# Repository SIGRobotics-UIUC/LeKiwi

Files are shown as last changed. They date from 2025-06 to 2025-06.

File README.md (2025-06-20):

# LeKiwi
<div style="display: flex; justify-content: center; align-items: center; padding: 25px;">
    
    
    
    
</div>

> LeKiwi - Low-Cost Mobile Manipulator | Version 1

  

## Step by step tutorial
1. [Bill of Materials](BOM.md)
2. [3D Printing](3DPrinting.md)
3. [Assembly](Assembly.md)
4. [Get started with LeRobot](https://huggingface.co/docs/lerobot/lekiwi)

## Hardware Design
#### Standardized Stacked Base Plates
- Inspired by the [open robotic platform](https://openroboticplatform.com/designrules), our base plates have 3.5mm diameter holes spaced 20mm apart for standardized mounting

#### Power
- (12V version) 12v 5A Li-ion battery
- (5V version) 65W Laptop power bank

> [!TIP]  
> If this is the first time you build robots please choose the 5V version as it’s a little bit easier to assemble. If you are more experienced and want to lift heavier objects choose the 12V version. If you want to cheapest option possible go for the wired LeKiwi version.

#### Compute
- Raspberry Pi 5
- Streaming to a Laptop

#### Drive
- 3-wheel Kiwi (holonomic) drive with omni wheels

#### Robot Arm
- [SO-ARM101](https://github.com/TheRobotStudio/SO-ARM100)

#### Sensors
- Workspace rgb camera
- Wrist rgb camera

## Software Capabilities
Goals:
- Teleoperation with controller or laptop WASD + leader arm
- Data collection pipeline
- Streaming joint angles and camera feed

## CAD Design
[Fusion 360 CAD](https://a360.co/4k1P8yO)

We also provide the [URDF](./URDF/) exported from CAD for simulation.
## Get In Touch!

Join the project on LeRobot's [Discord server](https://discord.gg/Jtz5TJtb2u) (channel `mobile-so100-arm`)! Let us know if you have any questions, suggestions, or other feedback.

## Check out our Dynamixel Version!
We converted LeKiwi to use ROBOTIS components by using the Koch v1.1 arm, U2D2 motor controller, and Dynamixel XL430 motors for the mobile base.  [Dynamixel LeKiwi](DynamixelLeKiwi)

## Main Contributors
Thank you to everyone who helped on the project!

**CAD Design**: Manav Chandaka, Bhargav Chandaka, Pepijn Kooijmans

**Software**: Pepijn Kooijmans, Gloria Wang, Bhargav Chandaka, Advait Patel

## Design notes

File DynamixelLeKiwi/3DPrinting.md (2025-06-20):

# 3D Printing
> **Estimated time:** ~34 hours

We provide ready-to-print STL files for the 3D-printed parts below. These can be printed with generic PLA filament on consumer-grade FDM printers. We tested on a [Bambu Lab P1S](https://us.store.bambulab.com/products/p1s) printer. For all components, we just load into bambuslicer, auto-rotate and auto-arrange, enable any recommended supports, and print.

## Parts

| Item | Quantity | Notes | 
|:---|:---:|:---:|
| [Base plate Top](/3DPrintMeshes/base_plate_layer2.stl) | 1 | |
| [Base plate Bottom](/3DPrintMeshes/base_plate_layer1.stl) | 1 | |
| [Dynamixel Drive motor mount](3DPrintMeshes/dynamixel_drive_motor_mount.stl) | 3 | |
| [Dynamixel Servo wheel hub](/3DPrintMeshes/dynamixel_wheel_hub.stl) | 3 | Use Supports<sup>[1](#footnote1)</sup> |
| [Servo controller mount](/3DPrintMeshes/servo_controller_mount.stl) | 1 | |
| [12v Battery mount](/3DPrintMeshes/battery_mount.stl) **or** [12v EU Battery mount](/3DPrintMeshes/battery_mount_eu.stl) **or** [5v Battery mount](/3DPrintMeshes/5v_specific/5v_power_bank_holder.stl)| 1 | |
| [RasPi case Top](/3DPrintMeshes/pi_case_top.stl) | 1 | <sup>[2](#footnote2)</sup> |
| [RasPi case Bottom](/3DPrintMeshes/pi_case_bottom.stl) | 1 | <sup>[2](#footnote2)</sup> |
| Arducam [base mount](/3DPrintMeshes/base_camera_mount.stl) | 1 | **Compatible with [this camera](https://www.amazon.com/Arducam-Camera-Computer-Without-Microphone/dp/B0972KK7BC)** |
| Webcam [base mount](3DPrintMeshes/webcam_mount/webcam_mount.stl), [gripper insert](3DPrintMeshes/webcam_mount/so100_gripper_cam_mount_insert.stl) | 1 | **Compatible with [this camera](https://www.amazon.fr/Vinmooog-equipement-Microphone-Enregistrement-conférences/dp/B0BG1YJWFN/)** |
| [Modified Follower Arm Base](/3DPrintMeshes/dynamixel_modified_base_arm.stl) | 1 | Use Tree Supports, **Optional, but recommended if you have not built Koch already** |
| [Follower arm](https://github.com/jess-moss/koch-v1-1) | 1 | |
| [Leader arm](https://github.com/jess-moss/koch-v1-1) | 1 | |

> **Note**: Make sure to enable supports where specified!
<!-- > STL files are already oriented and ready-to-print.  -->

## Printing Instructions
Assuming you already have access to a 3D printer<sup>[3](#footnote3)</sup>, follow these steps to print all the parts above.

### 1. Setup Printer
1. Calibrate the printer and level beds according to printer-specific instructions
2. Clean the print bed
3. Load-in filament

### 2. Print the Parts
1. Upload STL file to printing/slicing software. Auto-rotate and auto-arrange. 
2. Enable supports if specified and slice. We tested with the following settings:
    - Infill Density: 15%
    - Layer Height: 0.2 mm
    - Printing Speed: 150 mm/s
3. If needed, upload G-code (slice file) to printer and print

### 3. Take Down
1. Remove printed part(s) from printer
2. Clean print bed if needed
3. Remove any supports from printed parts

> For tutorials on how to assemble the robot, checkout the [Assembly](Assembly.md) page!

## Footnotes
<a name="footnote1">1</a>: Modified from [VEX VersaHub model](https://www.vexrobotics.com/versahubs.html?srsltid=AfmBOooDKLcAfkuEgHyrjk24WFDrLTP4TQWkGjEpC-9HcyaMMCUMDSzs)

<a name="footnote2">2</a>: Modified from [Micro Center model](https://www.printables.com/model/605060-raspberry-pi-5-case-wpower-button-v2)

<a name="footnote3">3</a>: If not, we recommend [Bambu Lab](https://bambulab.com/en-us) or [Prusa](https://www.prusa3d.com/), or checkout this [list of brands](https://github.com/ad-si/awesome-3d-printing?tab=readme-ov-file#3d-printer-brands).

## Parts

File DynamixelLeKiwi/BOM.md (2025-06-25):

# Bill of Materials

This page provides a complete list of parts needed to build the Dynamixel LeKiwi mobile manipulator. Our total cost is displayed in the table <sup>[1](#footnote1)</sup>.

| Price| US  | EU  | CN |
|---|----:|----:|----:|
| **Dynamixel LeKiwi** |  **$797.47**  |  **€1035.3**  |  **¥5938**  ||
| **Base only** |  **$320.47**  |  **€362.3**  |  **¥1991.28**  |

> [!NOTE] 
> Prices and items may vary depending on geographic location and time of purchase. If you find links for other countries or cheaper suppliers, please create an issue or PR so that we add them to the list!

### Mobile Base Structure:
| Part | Amount | Unit Cost (US) | Buy (US) | Unit Cost (EU) | Buy (EU) | Unit Cost (CN) | Buy (CN) |
| - | - | - | - | - | - | - | - |
| 4" Omni wheels | 3 | $9.99 | [VEX Robotics](https://www.vexrobotics.com/omni-wheels.html?srsltid=AfmBOorWdWT-FIiWSAbicYWSxqYr-d5X3CJSGxMkO33WO0thwlTn4DQu) | €24.5 | [RobotShop](https://eu.robotshop.com/products/100mm-omnidirectional-wheel-brass-bearing-rollers) |￥135 |[PDD](https://mobile.yangkeduo.com/goods.html?ps=kKWPC7xuzw "https://mobile.yangkeduo.com/goods.html?ps=kKWPC7xuzw")|
| M2 M3 M4 Assorted Screw Set | 1 | $14.99 | [Amazon](https://www.amazon.com/Button-Socket-Washers-Assortment-Machine/dp/B0BMQGJP3F) | €23.5 | [Amazon](https://www.amazon.fr/Cylindrique-Inoxydable-M2-Socket-Assortiment/dp/B09Y8WYFWD/) |￥25 |[Taobao（M2x5+M3套装+M3x10+M4x12）](https://e.tb.cn/h.64O1J2A9Is4pIJd "https://e.tb.cn/h.64O1J2A9Is4pIJd") |
| **Total** || **$44.96** || **€97** || **¥430** ||

### Sensors and Compute:

| Part| Amount | Unit Cost (US) | Buy (US) | Unit Cost (EU) | Buy (EU) |  Unit Cost (CN) | Buy (CN) |
|--|:-:|:-:|-|:-:|-|:-:|-|
| Raspberry Pi 5 (4GB)| 1 |$60.00| [Adafruit](https://www.adafruit.com/product/5812)| €57.00| [Mouser](https://eu.mouser.com/ProductDetail/Raspberry-Pi/SC1111?qs=HoCaDK9Nz5fnLhlMNnKTiQ%3D%3D)|￥410|[Taobao](https://e.tb.cn/h.64IIvlisvAL15g8?tk=fdOVexkHECW "https://e.tb.cn/h.64IIvlisvAL15g8?tk=fdOVexkHECW")|
| USB camera<sup>[2](#footnote2)</sup> | 2 | $12.98 | [Amazon](https://a.co/d/236G8Wn) | €12.00 | [Amazon](https://www.amazon.fr/Vinmooog-equipement-Microphone-Enregistrement-conf%C3%A9rences/dp/B0BG1YJWFN/) |￥48|[Taobao](https://e.tb.cn/h.64ILq3suMKATfUx?tk=IPSEexQAvxu "https://e.tb.cn/h.64ILq3suMKATfUx?tk=IPSEexQAvxu")|
| microSD card | 1 | $11.23 | [Amazon](https://www.amazon.com/SanDisk-Extreme-microSDXC-Memory-Adapter/dp/B09X7C7LL1/) | €10.00 | [Amazon](https://www.amazon.fr/Lexar-Carte-Micro-adaptateur-Smartphone/dp/B08XZ2KS1F)|￥58|[Taobao](https://e.tb.cn/h.64DMZzLz5h26s12?tk=eImPex96lCQ "https://e.tb.cn/h.64DMZzLz5h26s12?tk=eImPex96lCQ")|
| U2D2_INT | 1 | $32.10 | [ROBOTIS](https://en.robotis.com/shop_en/item.php?it_id=902-0132-000) | €27.93 | [ROBOTIS](https://en.robotis.com/shop_en/item.php?it_id=902-0132-000)|￥230.73|[ROBOTIS](https://en.robotis.com/shop_en/item.php?it_id=902-0132-000)|
| U2D2 PHB | 1 | $19.00 | [ROBOTIS](https://en.robotis.com/shop_en/item.php?it_id=902-0145-001) | €16.53 | [ROBOTIS](https://en.robotis.com/shop_en/item.php?it_id=902-0145-001)|￥136.57|[ROBOTIS](https://en.robotis.com/shop_en/item.php?it_id=902-0145-001)|
| **Total** ||  **$135.31**  ||  **€123.46** ||  **¥883.3** ||

### Other
| Part| Amount | Unit Cost (US) | Buy (US) | Unit Cost (EU) | Buy (EU) | Unit Cost (CN) | Buy (CN) |
|--|:-:|:-:|-|:-:|-|:-:|-|
| Table Clamp 4pcs | 1 | $18 | [Amazon](https://www.amazon.com/WORKPRO-Clamps-Woodworking-One-Handed-Spreader/dp/B0CQYDJWS8/) | € 21 | [Amazon](https://www.amazon.fr/dp/B08HW9VFM8/)| ¥10.8\*4  |[Taobao](https://e.tb.cn/h.64r5eomI6L59tBE?tk=gZWeex9fnlB "https://e.tb.cn/h.64r5eomI6L59tBE?tk=gZWeex9fnlB")|
| Screwdriver Set | 1 | $6 | [Amazon](https://www.amazon.com/Precision-Phillips-Screwdriver-Electronics-Computer/dp/B0DB227RTH) | €10 | [Amazon](https://www.amazon.fr/dp/B08ZXVMVYD/) | ￥20 |[Taobao](https://e.tb.cn/h.6ReL0wwgtPuSmNV?tk=3rLDV10AVtr)  |
| USB-C to USB-A Cable 2 pcs | 1 | $7 | [Amazon](https://www.amazon.com/Charging-etguuds-Charger-Braided-Compatible/dp/B0B8NWLLW2/?th=1) | €7 | [Amazon](https://www.amazon.fr/dp/B07BNF842T/) |￥17  |[Taobao](https://e.tb.cn/h.64HOv24RLmYC4Yh?tk=AXpgexkDFd4 "https://e.tb.cn/h.64HOv24RLmYC4Yh?tk=AXpgexkDFd4")|
| **Total** ||  **$31**  ||  **€38** || **¥80.20** ||

### Mobile Base Electronics
| Part | Amount | Unit Cost (US) | Buy (US) | Unit Cost (EU) | Buy (EU) | Unit Cost (CN) | Buy (CN) |
|:---|:---:|:---:|:---|:---:|---:|:-:|-|
| 12v 5a Battery | 1 | $32.99 | [Amazon](https://www.amazon.com/KBT-Rechargeable-Connector-Replacement-Security/dp/B0C242DYT1/ref=sr_1_2_sspa?) | €45.79 | [Amazon](https://www.amazon.fr/dp/B0D5QSMW21) | ￥70 |[Taobao](https://e.tb.cn/h.64IJNTnXwhn44BS?tk=PQQ8exkJEtR "https://e.tb.cn/h.64IJNTnXwhn44BS?tk=PQQ8exkJEtR")|
| Lever Wire Connector | 1 | $6.70 | [Amazon](https://www.amazon.com/Wago-221-413-LEVER-NUTS-Conductor-Connectors/dp/B06XGYXVXR/ref=sr_1_4) | €7.18 | [Amazon](https://www.amazon.fr/221-413-fil-électrique-connecteur-220-240-Terminal/dp/B01AKF3I58) | ￥3.50 |[Taobao](https://e.tb.cn/h.64r0Z6Y5jZczq5q?tk=XEaSex908q0 "https://e.tb.cn/h.64r0Z6Y5jZczq5q?tk=XEaSex908q0")|
| 12v 5a DC plug connector | 1 | $9.49 | [Amazon](https://www.amazon.com/43x2pcs-Connectors-Security-Lighting-MILAPEAK/dp/B072BXB2Y8/ref=sr_1_11) | €8.99 | [Amazon](https://www.amazon.fr/RUNCCI-YUN-Alimentation-dalimentation-Connecteur-Surveiller/dp/B0CX44HTKZ) | ￥3.10 |[Taobao](https://e.tb.cn/h.64IFOvrMdUVoQQX?tk=nahtexkvokE "https://e.tb.cn/h.64IFOvrMdUVoQQX?tk=nahtexkvokE")|
| 12v to 5v 5a USB-C converter | 1 | $9.99 | [Amazon](https://www.amazon.com/Klnuoxj-Converter-Interface-Waterproof-Compatible/dp/B0CRVW7N2J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) | €9.99 | [Amazon](https://www.amazon.fr/Greluma-convertisseur-Adaptateur-dalimentation-Compatible/dp/B0D7VDL2X6) | ￥20 |[1688](https://qr.1688.com/s/Eb6ykv4y "https://qr.1688.com/s/Eb6ykv4y") |
| DYNAMIXEL XL430-W250-T | 3 | $27.00 | [ROBOTIS](https://www.robotis.us/dynamixel-xl430-w250-t/) | €23.16 | [ROBOTIS](https://www.robotis.us/dynamixel-xl430-w250-t/)  | ￥193.76 |[ROBOTIS](https://www.robotis.us/dynamixel-xl430-w250-t/)|
| **Total** | | **$140.17** | | **€141.80** | | **￥677.88** | |

### Koch v1.1 2 Robot Arm Teleoperation Set 
Use  https://github.com/jess-moss/koch-v1-1 

#### Leader Arm
| Part | Amount | Unit Cost (US) | Buy US | Unit Cost (EU) | Buy EU | Unit Cost (UK) | Buy UK | Unit Cost (RMB) | Buy CN | Unit Cost (JPY) | Buy JP |
|---|---|---|---|---|---|---|---|---|---|---|---|
| Dynamixel XL330-M077-T | 6 | $24 | [Robotis](https://www.robotis.us/dynamixel-xl330-m077-t) | 40€ | [MyBotShop](https://www.mybotshop.de/DYNAMIXEL-XL330-M077-T)-[GenRobots](https://www.generationrobots.com/en/403818-dynamixel-xl330-m077-t-servo-motor.html) | £27 | [RoboSavvy](https://robosavvy.co.uk/robotis-dynamixel-xl330-m077-t.html) | ¥255 | [TaoBao](https://item.taobao.com/item.htm?id=651202518645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.) | ¥4,070 | [Robotis](https://e-shop.robotis.co.jp/product.php?id=416) |
| XL330 Frame and Idler Wheel 4pcs set<sup>[1](#myfootnote1)</sup> |  1 | $10 | [Robotis](https://www.robotis.us/fpx330-h101-4pcs-set) | 12€ | [MyBotShop](https://www.mybotshop.de/DYNAMIXEL-FPX330-H101-4PCS-Set)-[GenRobots](https://www.generationrobots.com/en/403860-FPX330-H101-hinge-frame-and-idler-set-dynamixel-xl330.html) | £10 |  [RoboSavvy](https://robosavvy.co.uk/fpx330-h101-4pcs-set.html) | ¥100 | [TaoBao](https://item.taobao.com/item.htm?id=646782958666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..) | ¥2,024 | [Robotis](https://e-shop.robotis.co.jp/product.php?id=437) |
| Waveshare Serial Bus Servo Driver Board | 1 | $10 | [Amazon](https://a.co/d/7C3RUYU) | 6€ | [Eckstein](https://eckstein-shop.de/WaveShare-Serial-Bus-Servo-Driver-Board-for-ST-SC-Serial-Bus-Servos-EN) | £11 | [Amazon](https://www.amazon.co.uk/Waveshare-Integrates-Control-Applicable-Integrate/dp/B0CJ6TP3TP/)| ¥24 | [TaoBao](https://item.taobao.com/item.htm?id=739743280684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) | n/a | n/a |
| 5V Power Supply | 1 | $6 | [Amazon](https://a.co/d/5u90NVp) | 9€ | [Amazon](https://www.amazon.fr/LEYF-Alimentation-Universelle-Adaptateur-Enfichable/dp/B09NGVWBSY) | £10 | [Amazon](https://www.amazon.co.uk/Adapter-Switching-100-240V-5-5x2-1mm-Transformer-5V2A-UKCA/dp/B0CH6HFVTK/)| ¥10 | [TaoBao](https://detail.tmall.com/item.htm?id=662655385028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) | ¥899 | [Amazon](https://a.co/d/5u90NVp) |
| Jumper Wires 3*40 pcs set (M-M, M-F, F-F) | 1 | $7 | [Amazon](https://a.co/d/hQfk2cb) | 9€ | [Amazon](https://www.amazon.fr/dp/B0BRMKX5RT/) | £5 | [Amazon](https://www.amazon.co.uk/dp/B09KGRM98K/)| ¥10 | [TaoBao](https://detail.tmall.com/item.htm?id=608543275703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) | n/a | n/a |
| Table Clamp | 1 | $6 | [Amazon](https://a.co/d/4KEiYdV) | n/a | n/a | £14 | [Amazon](https://www.amazon.co.uk/BESSEY-TOOLS-CM30-Forged-C-Clamp/dp/B0006694I2/?th=1)| ¥8 | [TaoBao](https://detail.tmall.com/item.htm?id=597606333219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..) | n/a | n/a |
| Table Clamp 4pcs set<sup>[2](#myfootnote2)</sup> | 1 | n/a | n/a | 14€ | [Amazon](https://www.amazon.fr/CAUTIOUS-Serre-Joint-R%C3%A9glable-Serre-Joints/dp/B0CJMB3SKH) | n/a | n/a | n/a | n/a | n/a | n/a |
| 1.5mm Star/Cruciform Screwdriver 2pcs set | 1 |  $7 | [Amazon](https://www.amazon.com/HARFINGTON-Precision-Screwdriver-Eyeglasses-Electronic/dp/B0D3XQ97XM/?th=1)| 7€ | [Amazon](https://www.amazon.fr/sourcing-map-Cruciforme-%C3%89lectroniques-R%C3%A9paration/dp/B0BQ69J2QF) | £4 | [Amazon](https://www.amazon.co.uk/sourcing-map-Screwdriver-Eyeglasses-Electronics/dp/B0BLM2Y2Z5/) | ¥2 | [TaoBao](https://detail.tmall.com/item.htm?id=790258857614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) | n/a | n/a |
| USB C-A or C-C 2pcs set<sup>[3](#myfootnote3)</sup> | 1 | $9 | [Amazon](https://www.amazon.com/Charging-etguuds-Charger-Braided-Compatible/dp/B0B8NWLLW2/) | 8€ | [Amazon](https://www.amazon.fr/dp/B08J7PQGD7/) | £6 | [Amazon](https://www.amazon.co.uk/Anker-Charger-Braided-Standard-Charging/dp/B07DD5YHMH/)| ¥12 | [TaoBao](https://detail.tmall.com/item.htm?id=44425281296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) | n/a | n/a |
| Total | | $199 | | 305€ | | £222 | | ¥1696 | | ¥6993 | |

#### Follower Arm

| Part | Amount | Unit Cost (US) | Buy US | Unit Cost (EU) | Buy EU | Unit Cost (UK) | Buy UK | Unit Cost (RMB) | Buy CN | Unit Cost (JPY) | Buy JP
|---|---|---|---|---|---|---|---|---|---|---|---|
| Dynamixel XL430-W250-T |  2 | $50 | [Robotis](https://www.robotis.us/dynamixel-xl430-w250-t) | 57-61€ | [MyBotShop](https://www.mybotshop.de/DYNAMIXEL-XL430-W250-T)-[GenRobots](https://www.generationrobots.com/en/402823-dynamixel-xl430-w250-t-servomotor.html) | £47 | [RoboSavvy](https://robosavvy.co.uk/dynamixel-xl430-w250-t.html) | ¥485 | [TaoBao](https://item.taobao.com/item.htm?id=588178867677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) | ¥6,831 | [Robotis](https://e-shop.robotis.co.jp/product.php?id=40)
| Dynamixel XL330-M288-T |  4 | $24  | [Robotis](https://www.robotis.us/dynamixel-xl330-m288-t) | 40-46€ | [MyBotShop](https://www.mybotshop.de/DYNAMIXEL-XL330-M288-T)-[GenRobots](https://www.generationrobots.com/en/403817-dynamixel-xl330-m288-t-servo-motor.html) | £27 | [RoboSavvy](https://robosavvy.co.uk/robotis-dynamixel-xl330-m288-t.html) | ¥255 | [TaoBao](https://item.taobao.com/item.htm?id=648175925849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) | ¥4,070 | [Robotis](https://e-shop.robotis.co.jp/product.php?id=417)
| XL330 Frame and Idler Wheel 4pcs set<sup>[1](#myfootnote1)</sup> |  1 | $10 | [Robotis](https://www.robotis.us/fpx330-h101-4pcs-set) | 12€ | [MyBotShop](https://www.mybotshop.de/DYNAMIXEL-FPX330-H101-4PCS-Set)-[GenRobots](https://www.generationrobots.com/en/403860-FPX330-H101-hinge-frame-and-idler-set-dynamixel-xl330.html) | £10 |  [RoboSavvy](https://robosavvy.co.uk/fpx330-h101-4pcs-set.html) | ¥100 | [TaoBao](https://item.taobao.com/item.htm?id=646782958666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..) | ¥2,024 | [Robotis](https://e-shop.robotis.co.jp/product.php?id=437) |
| XL430 Idler Wheel set | 1 | $7 | [Robotis](https://www.robotis.us/hn11-i101-set) | 9€ | [MyBotShop](https://www.mybotshop.de/DYNAMIXEL-XL430-HN11-I101-Set)-[GenRobots](https://www.generationrobots.com/en/403206-hn11-i101-horn-set.html) | £7 | [Robosavvy](https://robosavvy.co.uk/hn11-i101-set.html)| ¥75 | [TaoBao](https://item.taobao.com/item.htm?id=581922883001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..) | ¥836 | [Robotis](https://e-shop.robotis.co.jp/product.php?id=147)
| Waveshare Serial Bus Servo Driver Board | 1 | $10 | [Amazon](https://a.co/d/7C3RUYU) | 6€ | [Eckstein](https://eckstein-shop.de/WaveShare-Serial-Bus-Servo-Driver-Board-for-ST-SC-Serial-Bus-Servos-EN) | £11 | [Amazon](https://www.amazon.co.uk/Waveshare-Integrates-Control-Applicable-Integrate/dp/B0CJ6TP3TP/)| ¥24 | [TaoBao](https://item.taobao.com/item.htm?id=739743280684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) | n/a | n/a |
| Voltage Reducer | 1 | $14 | [Amazon](https://www.amazon.com/EPLZON-Converter-5V-5-3V-Transformer-Regulator/dp/B09R4DBZJK) | 14€ | [Amazon](https://www.amazon.fr/dp/B0B58T2YY8/) | £15 | [Amazon](https://www.amazon.co.uk/Converter-Voltage-Regulator-Transformer-Charging/dp/B0989DKYWN) | ¥11 | [TaoBao](https://detail.tmall.com/item.htm?id=617425895508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) | n/a | n/a |
| 12V Power Supply | 1 | $12 | [Amazon](https://a.co/d/40o8uMN) | 15-36€ | [Amazon](https://www.amazon.fr/LEDMO-Alimentation-Adaptateur-Transformateurs-Chargeur/dp/B07PGLXK4X)-[GenRobots](https://www.generationrobots.com/en/400866-smps-charger-for-bioloid-and-dynamixel-robotis.html) | £13 | [Amazon](https://www.amazon.co.uk/Facmogu-Adapter-100-240V-Monitors-Amplifier/dp/B0CXPMJJMF/) | ¥20 | [TaoBao](https://detail.tmall.com/item.htm?id=678305663026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) | ¥1,685 | [Amazon](https://a.co/d/40o8uMN) |
| Jumper Wires 3*40 pcs set (M-M, M-F, F-F) | 1 | $7 | [Amazon](https://a.co/d/hQfk2cb) | 9€ | [Amazon](https://www.amazon.fr/dp/B0BRMKX5RT/) | £5 | [Amazon](https://www.amazon.co.uk/dp/B09KGRM98K/)| ¥10 | [TaoBao](https://detail.tmall.com/item.htm?id=608543275703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) | n/a | n/a |
| Table Clamp | 1 | $6 | [Amazon](https://a.co/d/4KEiYdV) | n/a | n/a | £14 | [Amazon](https://www.amazon.co.uk/BESSEY-TOOLS-CM30-Forged-C-Clamp/dp/B0006694I2/?th=1) | ¥8 | [TaoBao](https://detail.tmall.com/item.htm?id=597606333219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..) | n/a | n/a |
| Table Clamp 4pcs set<sup>[4](#myfootnote4)</sup> | 1 | n/a | n/a | 14€ | [Amazon](https://www.amazon.fr/CAUTIOUS-Serre-Joint-R%C3%A9glable-Serre-Joints/dp/B0CJMB3SKH) | n/a | n/a | n/a | n/a | n/a | n/a |
| 1.5mm Star/Cruciform Screwdriver 2pcs set<sup>[4](#myfootnote5)</sup> | 1 |  $7 | [Amazon](https://www.amazon.com/HARFINGTON-Precision-Screwdriver-Eyeglasses-Electronic/dp/B0D3XQ97XM/?th=1)| 7€ | [Amazon](https://www.amazon.fr/sourcing-map-Cruciforme-%C3%89lectroniques-R%C3%A9paration/dp/B0BQ69J2QF) | £4 | [Amazon](https://www.amazon.co.uk/sourcing-map-Screwdriver-Eyeglasses-Electronics/dp/B0BLM2Y2Z5/) | ¥2 | [TaoBao](https://detail.tmall.com/item.htm?id=790258857614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) | n/a | n/a |
| USB C-A or C-C 2pcs set<sup>[6](#myfootnote6)</sup> | 1 | $9 | [Amazon](https://www.amazon.com/Charging-etguuds-Charger-Braided-Compatible/dp/B0B8NWLLW2/) | 8€ | [Amazon](https://www.amazon.fr/dp/B08J7PQGD7/) | £6 | [Amazon](https://www.amazon.co.uk/Anker-Charger-Braided-Standard-Charging/dp/B07DD5YHMH/)| ¥12 | [TaoBao](https://detail.tmall.com/item.htm?id=44425281296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) | n/a | n/a |
| Total | | $278 | | 368€ | | £285 | | ¥2251 | | ¥15446 | |

> Head to [3D Printing](3DPrinting.md) for the next step!

<br></br>

## Footnotes
<a name="footnote1">1</a>: Doesn't include cost of 3D printing

<a name="footnote2">2</a>: Another supported camera option is the Arducam 5MP Wide Angle found [here](https://www.amazon.com/Arducam-Camera-Computer-Without-Microphone/dp/B0972KK7BC)

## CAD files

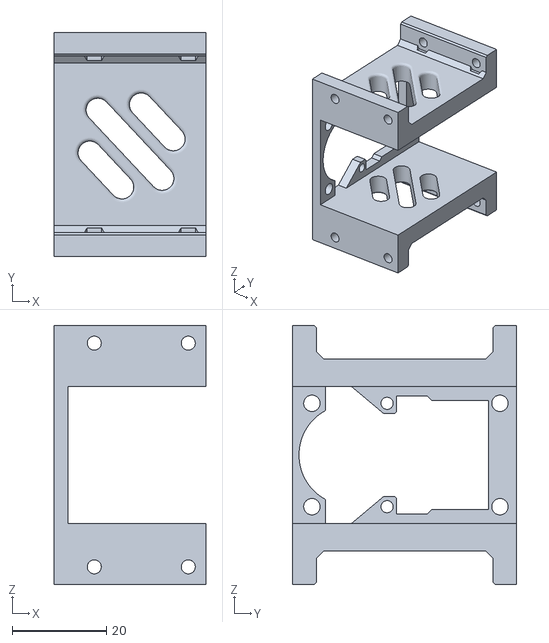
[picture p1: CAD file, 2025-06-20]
3DPrintMeshes/dynamixel_specific/dynamixel_drive_motor_mount.stl
32.3 x 47.6 x 55.1

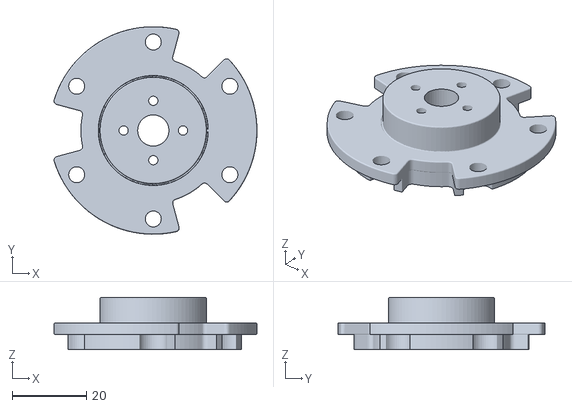
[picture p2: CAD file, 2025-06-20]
3DPrintMeshes/dynamixel_specific/dynamixel_wheel_hub .stl
54.7 x 55.9 x 14.0

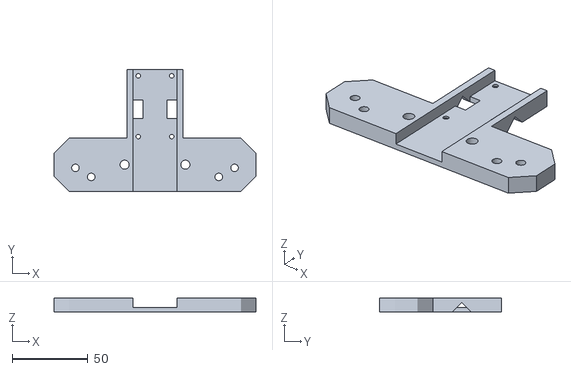
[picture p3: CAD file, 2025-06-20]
3DPrintMeshes/dynamixel_specific/dynamixel_modified_base_arm.stl
133.0 x 80.0 x 9.00

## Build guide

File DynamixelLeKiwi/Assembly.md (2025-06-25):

# Assembly
> **Estimated time:** 2 hours

*Exact component placements can be visualized in the [Fusion360 Online CAD](https://a360.co/4iD2gtf)*

*We assume you already have a [Koch Arm](https://github.com/jess-moss/koch-v1-1) built*
### 1. Assemble Wheel Modules (3 per robot)

1. Attach the drive motor to the motor mount using 4 m2x5 tap screws.

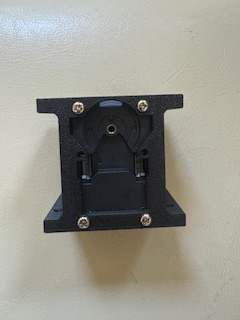
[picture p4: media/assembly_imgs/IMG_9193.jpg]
    

2. Screw the drive motor mount onto the bottom base plate using 4 m3x12 machine screws.

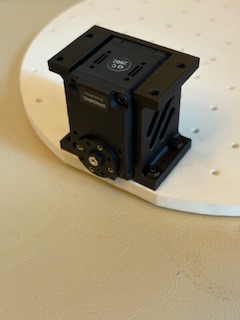
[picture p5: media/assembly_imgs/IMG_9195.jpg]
    

3. Attach the wheel hub to the omniwheel using 2 m4x12 machine screws.

    

4. Attach the wheel hub to the servo horn using 4 m3x16 machine screws.

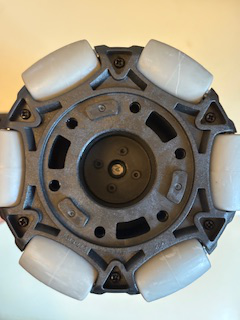
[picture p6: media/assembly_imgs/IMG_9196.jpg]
    
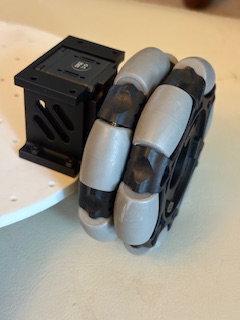
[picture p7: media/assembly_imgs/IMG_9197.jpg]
    

### 2. Bottom Plate Assembly
1. Insert m3 nuts into the mounts for the servo controller and battery mounts. Screw both onto the bottom base plate with 4 m3x12 machine screws.

2. Add the servo driver and attach the wires to the 3 drive servos.

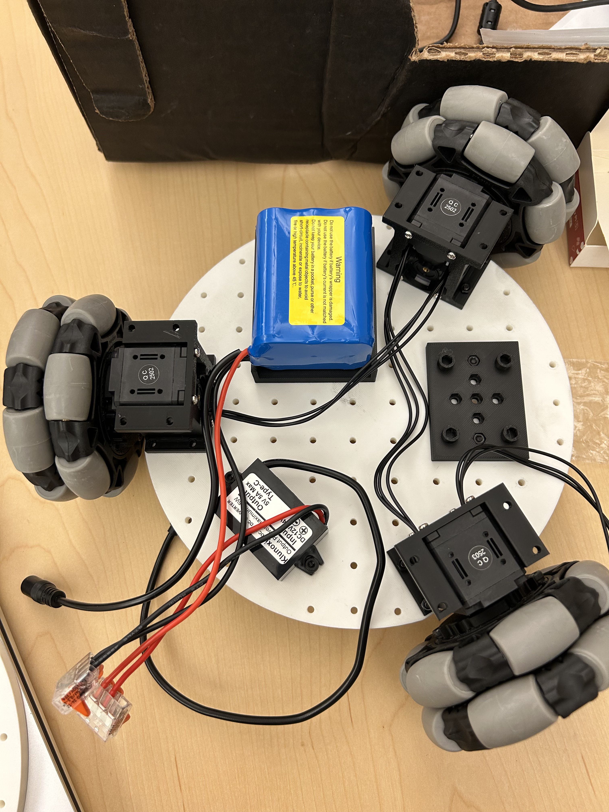
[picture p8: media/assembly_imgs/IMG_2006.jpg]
    
3. Wiring Electronics
   -    Use the wago lever connectors to connect the ground and power battery wire leads to the leads of the 12v->5v converter and the dc barrel plug adapter. Screw on the 12v to 5v converter to the bottom base plate with 2 m3x16 machine screws and 2 m3 nuts.

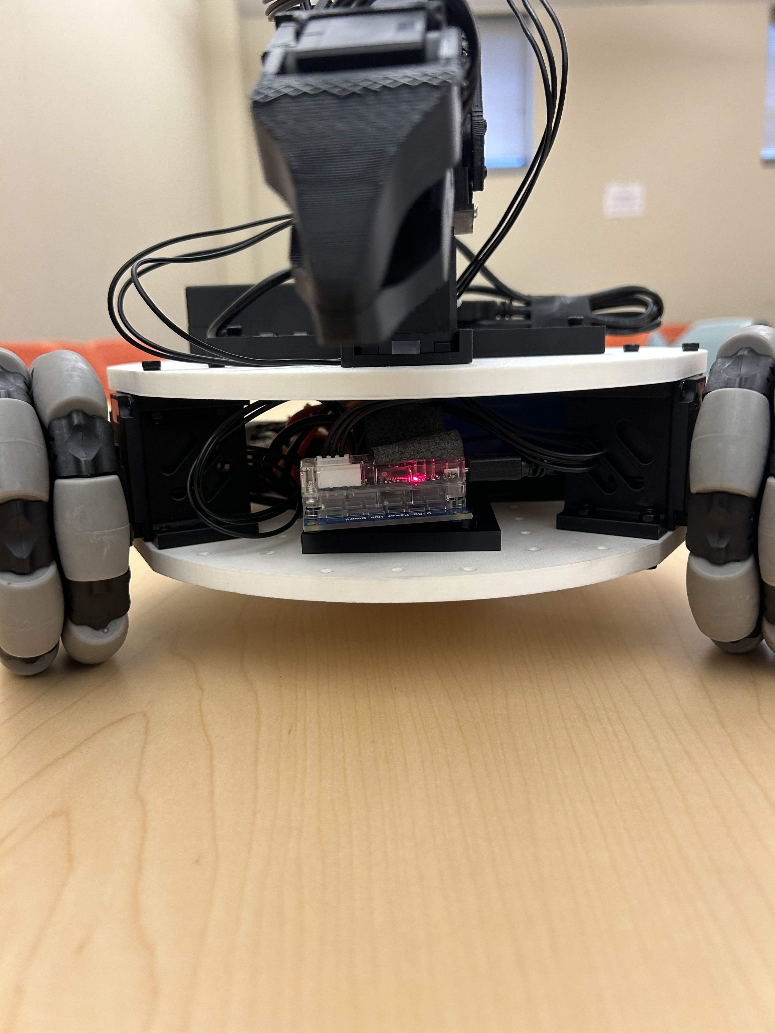
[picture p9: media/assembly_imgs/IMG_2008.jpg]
         

### 3. Top plate Assembly
1. Place the raspberry pi 5 into the pi case bottom and snap on the top part of the case. 
2. Attach the Pi to the top base plate using 2 m3x12 machine screws and mount the SO-101 arm with 4 m3x20 machine screws. Using our modified SO-101 base or the original will work as there are holes for both in the plate.

    

### 4. Final Assembly
1. Feed the servo controller usb-c to usb-a, 5v usb-c power, and SO0-101 servo wires through the hole in the top base plate. 

    

2. Mount the top base plate onto the motor mounts using 4 m3x12 machine screws.

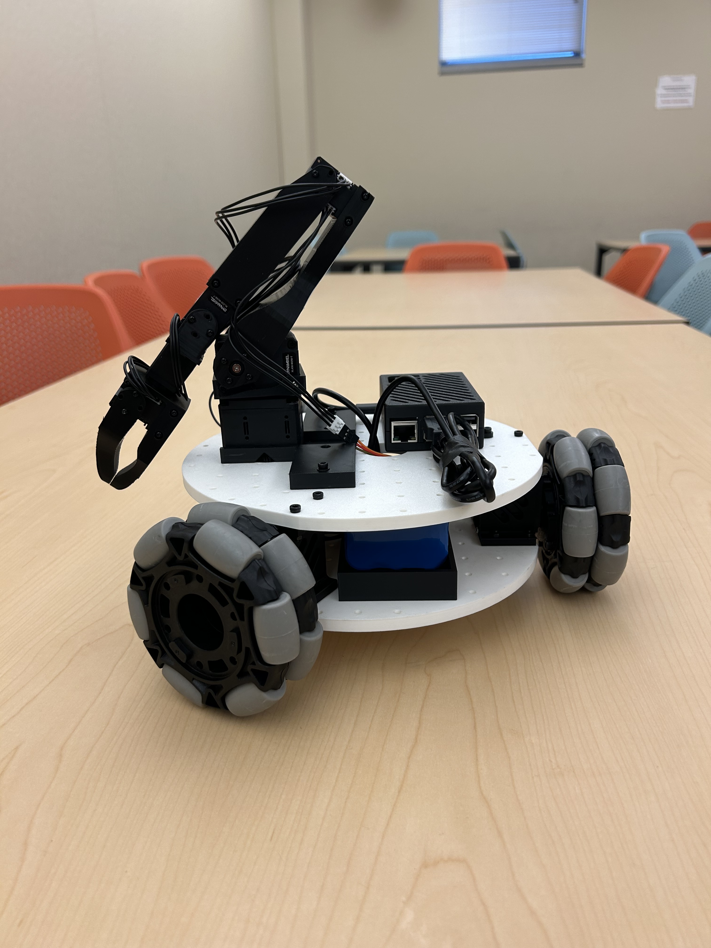
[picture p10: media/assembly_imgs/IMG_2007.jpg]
    

### 5: Attach Cameras
*Note: The mounts we designed are specific to the cameras we chose. They may need to be modified for different camera modules.*
#### (Option 1) Mounting Arducam
For these [camera's](https://www.amazon.com/Arducam-Camera-Computer-Without-Microphone/dp/B0972KK7BC) you can print these parts 1x `3DPrintMeshes/base_camera_mount.stl` 
1. Screw the base camera mount onto the bottom base plate(attach the arducam 5MP wide angle camera to the mount with 2 m2.5x12 machine screws). The cable for the camera mount can also be fed through the cutout

    

### Plug everything in and its ready!
Power the electronics by plugging in the DC barrel plug adapter to the servo motor controller and the 5v usb-c connector to the raspberry pi 5. The usb cables from the servo controller and the cameras can directly be plugged in to the raspberry pi.

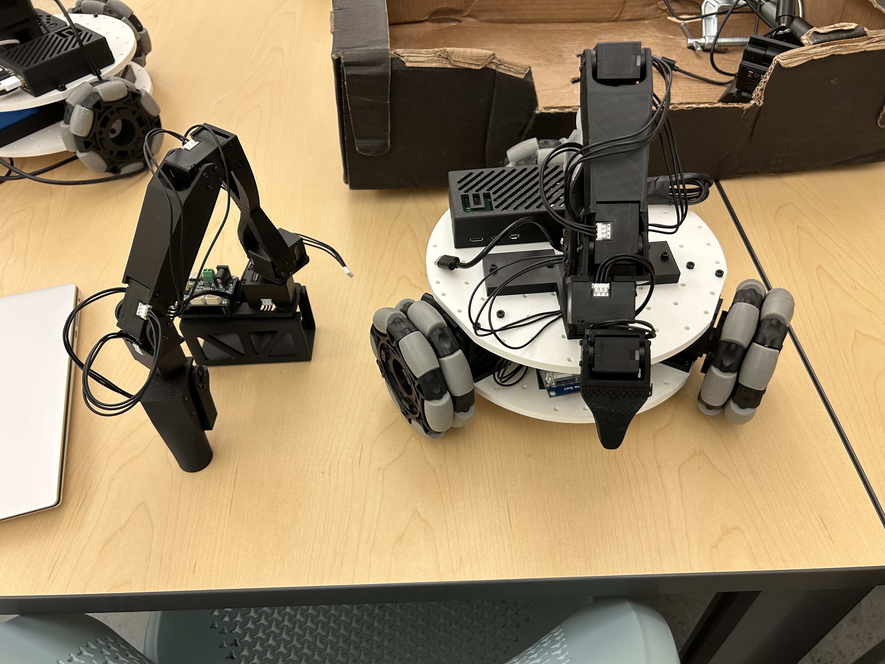
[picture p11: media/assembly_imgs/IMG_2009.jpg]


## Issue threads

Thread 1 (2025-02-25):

Is the 12v ST3215 used by the arm and the base the same servo?

timqian, 2025-02-25:
The name and params of the servos look the same, but they have different links and price

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

GCrequer, 2025-03-20:
Hi ! Are these 2 servo continuous ? I mean, not restricted to a 0-360° or 0-180° range ? And maybe with a speed-servoing option (can be emulated easily otherwise) ?

Closed 2025-02-26.

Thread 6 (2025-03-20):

12V EU bom links to a 3A DC-DC instead of a 5A

joostwestra, 2025-03-20:
Current link:
https://www.amazon.fr/Greluma-convertisseur-Adaptateur-dalimentation-Compatible/dp/B0D7VDL2X6

joostwestra, 2025-03-26:
This issue will probably solved by the alignment of the 5V and 12V diagrams?

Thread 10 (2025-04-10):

SO100 arm is very jittery

fuzzie360, 2025-04-10:
In my build the SO100 arm is very jittery at static positions while on the robot. I changed from battery power to a PSU but the behavior did not change.

Only the arm is affected by this, the wheel base is working fine.

You can see from this video the arm visibly and audibly shaking:

https://github.com/user-attachments/assets/bcad7061-50c0-4050-8a41-a064ff616c37

What am I doing wrong?

fuzzie360, 2025-04-10:
Hmmm, going to answer my own question, I found that the PID coefficients in the arm need tuning.

Stock coefficients for motor 1:

```
P=32
I=0
D=32
```

After changing them to:
```
P=16
I=0
D=32
```
I found the robot to be much less shaky. I'll continue fine tuning them until I get good results through the arm.

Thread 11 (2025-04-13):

3D print list shows old motor mount

jccalvojackson, 2025-04-13:
the 3d print list shows old motor mount https://github.com/SIGRobotics-UIUC/LeKiwi/blob/main/3DPrinting.md
Same with the [assembly](https://github.com/SIGRobotics-UIUC/LeKiwi/blob/main/Assembly.md#assembly) fusion 360 model

jccalvojackson, 2025-04-14:
closed by this https://github.com/SIGRobotics-UIUC/LeKiwi/commit/a1623f3e2a193184f4ebdbd36aecbfe4592b3c94

Closed 2025-04-14.

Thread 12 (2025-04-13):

EU 12V battery is different than the US one

jccalvojackson, 2025-04-13:
In the [BOM](https://github.com/SIGRobotics-UIUC/LeKiwi/blob/main/BOM.md#mobile-base-electronics-12v), the [EU Battery](https://www.amazon.fr/NASTIMA-lithium-ion-Rechargeable-Cam%C3%A9scopes-%C3%A9lectronique/dp/B09FK4ZDSL) is different than the one in the [US link](https://www.amazon.com/KBT-Rechargeable-Connector-Replacement-Security/dp/B0C242DYT1/ref=sr_1_2_sspa?). In particular, the cable terminals and dimensions are different. This last point makes it incompatible with the 3d battery mount

## US
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

## EU
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

jccalvojackson, 2025-04-14:
closed by https://github.com/SIGRobotics-UIUC/LeKiwi/commit/0df14e7371ff8d96b038d1bf3ddb90bd2072acbd

Closed 2025-04-14.

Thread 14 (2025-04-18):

URDF file needs updating with new motor mounts

fuzzie360, 2025-04-18:
Hello, I am using the URDF file for my ROS2 installation. I want to contribute some improvements to the URDF file but it seems computer generated and I do not know how to regenerate it.

Current issues with the URDF I am looking to fix:

- Way too complex with unnecessary links for mounts and other useless geometry
- Robot is not using industry standard axes (X should be forward)
- Revolute joins seems reversed
- No base transform to the ground (if you use the base as the base link the robot is inside the ground)

Vector-Wangel, 2025-04-20:
Similar problem here. I want to modify the new motor mount model but it's only in stl, also the design in fusion360 online CAD is not updated.

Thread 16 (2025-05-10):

Loading 5v_power_bank_holder.stl in BambuStudio results in error

eric54321, 2025-05-10:
Loading 5v_power_bank_holder.stl in BambuStudio for Bambu A1 results in error:

Error.  Loading of a model file failed.

Warning.  The file does not contain any geometry data.

eric54321, 2025-05-18:
Nevermind, user error

Closed 2025-05-18.

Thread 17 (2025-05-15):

Change the base camera mount so it can support innomaker cameras

vladfatu, 2025-05-15:
I use an innomaker camera(https://www.amazon.de/dp/B0CLRJZG8D) instead of arducam and the base mount fits perfectly with the exception of the cutout that needs to be on the opposite side.

I changed the stl for myself so it can fit both, but I think this could help other people as well considering that innomaker is the camera recommendation in the SO-ARM100 project.

I will make a pull request with it and reference this issue it if that's ok.

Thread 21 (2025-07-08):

3mf file doesn't open

DipFlip, 2025-07-08:
I'm trying to print the files but can't seem to open the 3mf file in any program. In cura I get this for instance:

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

Closed 2025-07-08.

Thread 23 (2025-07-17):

Unable to teleoperate

LaurentBerger, 2025-07-17:
I followed doc.

I ran on raspberry :
`python -m lerobot.robots.lekiwi.lekiwi_host --robot.id=my_awesome_kiwi`
and on desktop computer
`python examples/lekiwi/teleoperate.py`

result on desktop
is

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

and result on raspberry
```
 python -m lerobot.robots.lekiwi.lekiwi_host --robot.id=my_awesome_kiwi
Move robot to the middle of its range of motion and press ENTER....
Move all arm joints except '['arm_wrist_flex', 'arm_wrist_roll', 'base_left_wheel', 'base_back_wheel', 'base_right_wheel']' sequentially through their entire ranges of motion.
Recording positions. Press ENTER to stop...

-------------------------------------------
-------------------------------------------
NAME            |    MIN |    POS |    MAX7
arm_shoulder_pan |    947 |   1979 |   30672
arm_shoulder_lift |    961 |    971 |   3082
arm_elbow_flex  |    881 |   2935 |   2936
arm_gripper     |   2015 |   2047 |   2903
Calibration saved to /home/kiwi/.cache/huggingface/lerobot/calibration/robots/lekiwi/None.json
WARNING:root:No command available
WARNING:root:No command available
WARNING:root:No command available
WARNING:root:No command available
WARNING:root:No command available
WARNING:root:No command available
WARNING:root:No command available
WARNING:root:No command available
WARNING:root:Command not received for more than 500 milliseconds. Stopping the base.
WARNING:root:No command available
WARNING:root:No command available
WARNING:root:No command available
WARNING:root:No command available
WARNING:root:No command available
WARNING:root:No command available
WARNING:root:No command available
WARNING:root:No command available
WARNING:root:No command available
WARNING:root:No command available
WARNING:root:No command available
WARNING:root:No command available
WARNING:root:No command available
WARNING:root:No command available
WARNING:root:No command available
WARNING:root:No command available
WARNING:root:No command available
WARNING:root:No command available
WARNING:root:No command available
WARNING:root:No command available
WARNING:root:No command available
WARNING:root:No command available
WARNING:root:No command available
WARNING:root:No command available
WARNING:root:No command available
WARNING:root:No command available
WARNING:root:No command available
WARNING:root:No command available
WARNING:root:No command available
WARNING:root:No command available
WARNING:root:No command available
WARNING:root:No command available
WARNING:root:No command available
WARNING:root:Command not received for more than 500 milliseconds. Stopping the base.
WARNING:root:No command available
WARNING:root:No command available
WARNING:root:No command available
WARNING:root:No command available
WARNING:root:No command available
WARNING:root:No command available
WARNING:root:No command available
WARNING:root:No command available
WARNING:root:No command available
WARNING:root:No command available
WARNING:root:No command available
WARNING:root:No command available
WARNING:root:No command available
WARNING:root:Command not received for more than 500 milliseconds. Stopping the base.
WARNING:root:No command available
WARNING:root:No command available
WARNING:root:No command available
WARNING:root:No command available
WARNING:root:No command available
WARNING:root:No command available
WARNING:root:Command not received for more than 500 milliseconds. Stopping the base.
WARNING:root:No command available
WARNING:root:No command available
WARNING:root:No command available
WARNING:root:No command available
WARNING:root:No command available
WARNING:root:No command available
WARNING:root:No command available
WARNING:root:No command available
Cycle time reached.
Shutting down Lekiwi Host.

```

What's wrong? If I moved leader arm or kiwi using keyboard kiwi is shutting down

pkooij, 2025-07-18:
I think you have to increase the  connection_time_s: int = 300 in config_lekiwi.py

LaurentBerger, 2025-07-19:
Thanks
I changed

in
```
    # Duration of the application
    connection_time_s: int = 300

    # Watchdog: stop the robot if no command is received for over 0.5 seconds.
    watchdog_timeout_ms: int = 2000

    # If robot jitters decrease the frequency and monitor cpu load with `top` in cmd
    max_loop_freq_hz: int = 10

```
in desktop computer and in raspberry. Which one is process?

Now in rerun I quit the session. I have got this warning message in windows console:
```
python examples/lekiwi/teleoperate.py
[2025-07-19T09:42:58Z WARN  re_sdk_comms::server] Closing connection to client at 127.0.0.1:50812: Une connexion établie a été abandonnée par un logiciel de votre ordinateur hôte. (os error 10053)

```
then I tried CTRL+c but it does not work. I must use task manager to kill command window

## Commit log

2025-06-20 Updated README and completed dynamixel LeKiwi branch
    [dynamixel_drive_motor_mount.stl, dynamixel_modified_base_arm.stl, dynamixel_wheel_hub .stl]
2025-06-20 Fixed assembly images
2025-06-20 Fixed Dynamixel Assembly
2025-06-25 Fixed Motor Pricing
2025-06-25 Updated assembly motor references
